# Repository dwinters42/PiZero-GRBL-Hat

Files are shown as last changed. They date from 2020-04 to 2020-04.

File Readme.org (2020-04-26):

#+TITLE:  Pi Zero GRBL hat

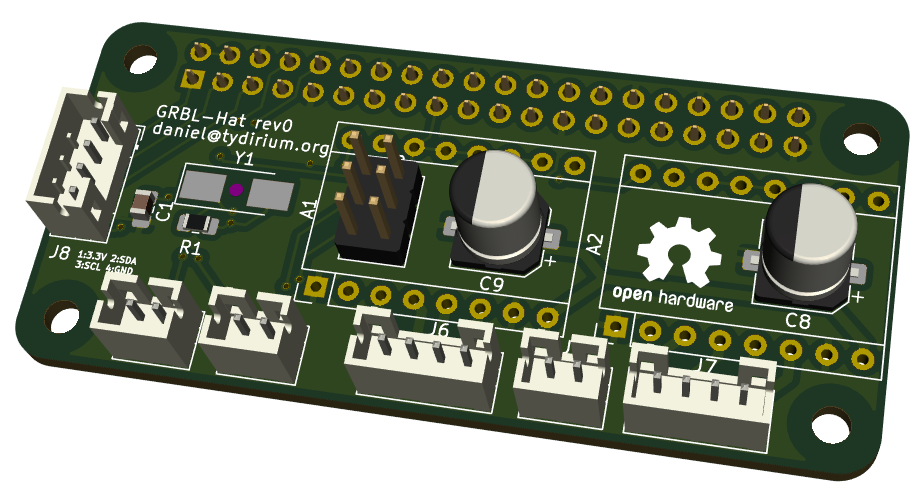
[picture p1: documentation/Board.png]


This is a RaspberryPi Zero-compatible add-on board that can be used to
control up to 2 stepper motors using GCode commands. The board works
with the non-Wifi (Pi Zero) and the Wifi version (Pi Zero W). It
should also work with a standard Raspberrypi, although I have not
tested this.

The hat has an on-board AVR Mega328P micro-controller that runs the
[[https://github.com/grbl/grbl][GRBL]] firmware, 2 sockets for Pololu-compatible Stepper boards
(e.g. DRV8825 and compatible) and connectors for the stepper motors,
limit switches, stepper motor power and an extra I2C connector that is
wired to the Pi Zero I2C contacts.

The big benefit of this arrangement is that the AVR takes care of all
the timing-sensitive tasks, so that the Raspberry Pi can do other
things.

* Building instructions
** Get components

See the bill of materials below.

** Assemble board

Use the brilliant interactive [[file:documentation/bom_interactive.html][HTML-BOM]] generated by the brilliant [[https://github.com/openscopeproject/InteractiveHtmlBom][BOM
KICAD plugin]] from openscopeproject to populate the board.

** Program firmware on AVR

Make sure the populated board is not connected to the Raspberrypi. Use
the ICSP connector on the front of the board to upload the GRBL
firmware using e.g. avrdude and a compatible programmer.

** Mount the board

With the Raspberrypi turned off, plug the GRBL hat board into the Pi
header, so that the 2 boards are aligned to each other. Do not connect
anything to the GRBL hat yet.

** Set up Pi Zero

In order for the communication to work, the on-board serial board of
the Raspberrypi has to be enabled with raspi-config: run raspi-config
in a terminal, go to Interfacing Options -> Serial -> No to login
shell -> Yes to enable serial port hardware. After rebooting, you
should have a new serial port accessible as /dev/ttyS0.

** Test serial connection

Connect to Grbl using the serial terminal of your choice. Set
the port to /dev/ttyS0 and the the baud rate to 115200, 8 bits, no
parity, 1 stop bit (8N1). One possibility is to use miniterm:

#+begin_example
  miniterm /dev/ttyS0 115200
#+end_example

Once connected, you will not see anything (GRBL started when the Pi
was plugged into power).

Type $ and press enter to have GRBL print a help message. You should
not see any local echo of the $ and enter. Grbl should respond with:

#+begin_example
  [HLP:$$ $# $G $I $N $x=val $Nx=line $J=line $SLP $C $X $H ~ ! ? ctrl-x]
  ok
#+end_example

Congratulations, you have a working GRBL controller connected to your
Pi Zero!

Shut down the Pi and disconnect power. Next, connect two stepper
driver boards (e.g. 2x Pololu DRV8825 driver board). Make sure you get
the orientation correct.

Then connect the motor power supply and set the current using the
trimpot on the driver boards. Disconnect motor power, plug in 2
stepper motors (e.g. NEMA17 form factor) and apply motor power again.

** First trial run

Turn on power to the Pi and log in via ssh. Run the following commands
from a terminal to test the motors:

#+begin_example
  stty -F /dev/ttyS0 115200 # set baud rate to 115200 baud
  cat testing/test.gcode > /dev/ttyS0
#+end_example

This should move first the x-axis to 45 degrees and back, followed by
the y-axis. If there is jerky motion or no motion at all, make sure
that the wire connections to the steppers are good.

* Using the board

The Raspberrypi board communicates with the GRBL controller over the
on-board serial port /dev/ttyS0. The serial port needs to be
configured to 115200 baud, 8 databits, 1 stopbit, no parity (8N1).

The stepper resolution is set to 32 microsteps in hardware, this
cannot be changed. For a standard stepper with 200 steps per
revolution this gives 200*32/360 = 17.778 steps per degree.

Look at the [[https://github.com/gnea/grbl/wiki][GRBL wiki]] for any GRBL related questions.

* Bill of materials

| *Ref* | *Qty* | *Value*          | *Part*                      | *Mouser part*     |
|-------+-------+------------------+-----------------------------+-------------------|
| A1    |     1 | AXIS_X           | Pololu DRV8825 module       |                   |
| A2    |     1 | AXIS_Y           | Pololu DRV8825 module       |                   |
| C1 C2 |     2 | 100n 0805        |                             |                   |
| C4 C5 |     2 | 33p 0805         |                             |                   |
| C8 C9 |     2 | 100u dia 6.3 25V |                             |                   |
| J1    |     1 | GPIO_CONNECTOR   | pin header 2x20             |                   |
| J2    |     1 | ISP              | pin header 2x03             |                   |
| J3    |     1 | LIMIT_X          | JST PH B2B 1x02 vert        |                   |
| J4    |     1 | LIMIT_Y          | JST PH B2B 1x02 vert        |                   |
| J5    |     1 | VMOT             | JST PH B2B 1x02 vert        |                   |
| J6    |     1 | MOTOR_X          | JST PH B2B 1x04 vert        |                   |
| J7    |     1 | MOTOR_Y          | JST PH B2B 1x04 vert        |                   |
| J8    |     1 | I2C              | JST PH B2B 1x04 vert        |                   |
| R1    |     1 | 1M 0805          |                             |                   |
| R2    |     1 | 10K 0805         |                             |                   |
| U1    |     1 | uC TQFP-32       | Microchip ATmega328P-AU     | 556-ATMEGA328P-AU |
| Y1    |     1 | 16MHz ABM3       | Abracon ABM3-16.000MHZ-B2-T | 815-ABM3-16-D2Y-T |

* Todos for next revision

- [ ] use less pins on the Raspi connector + cutout in PCB
- [ ] add photos of the finished board

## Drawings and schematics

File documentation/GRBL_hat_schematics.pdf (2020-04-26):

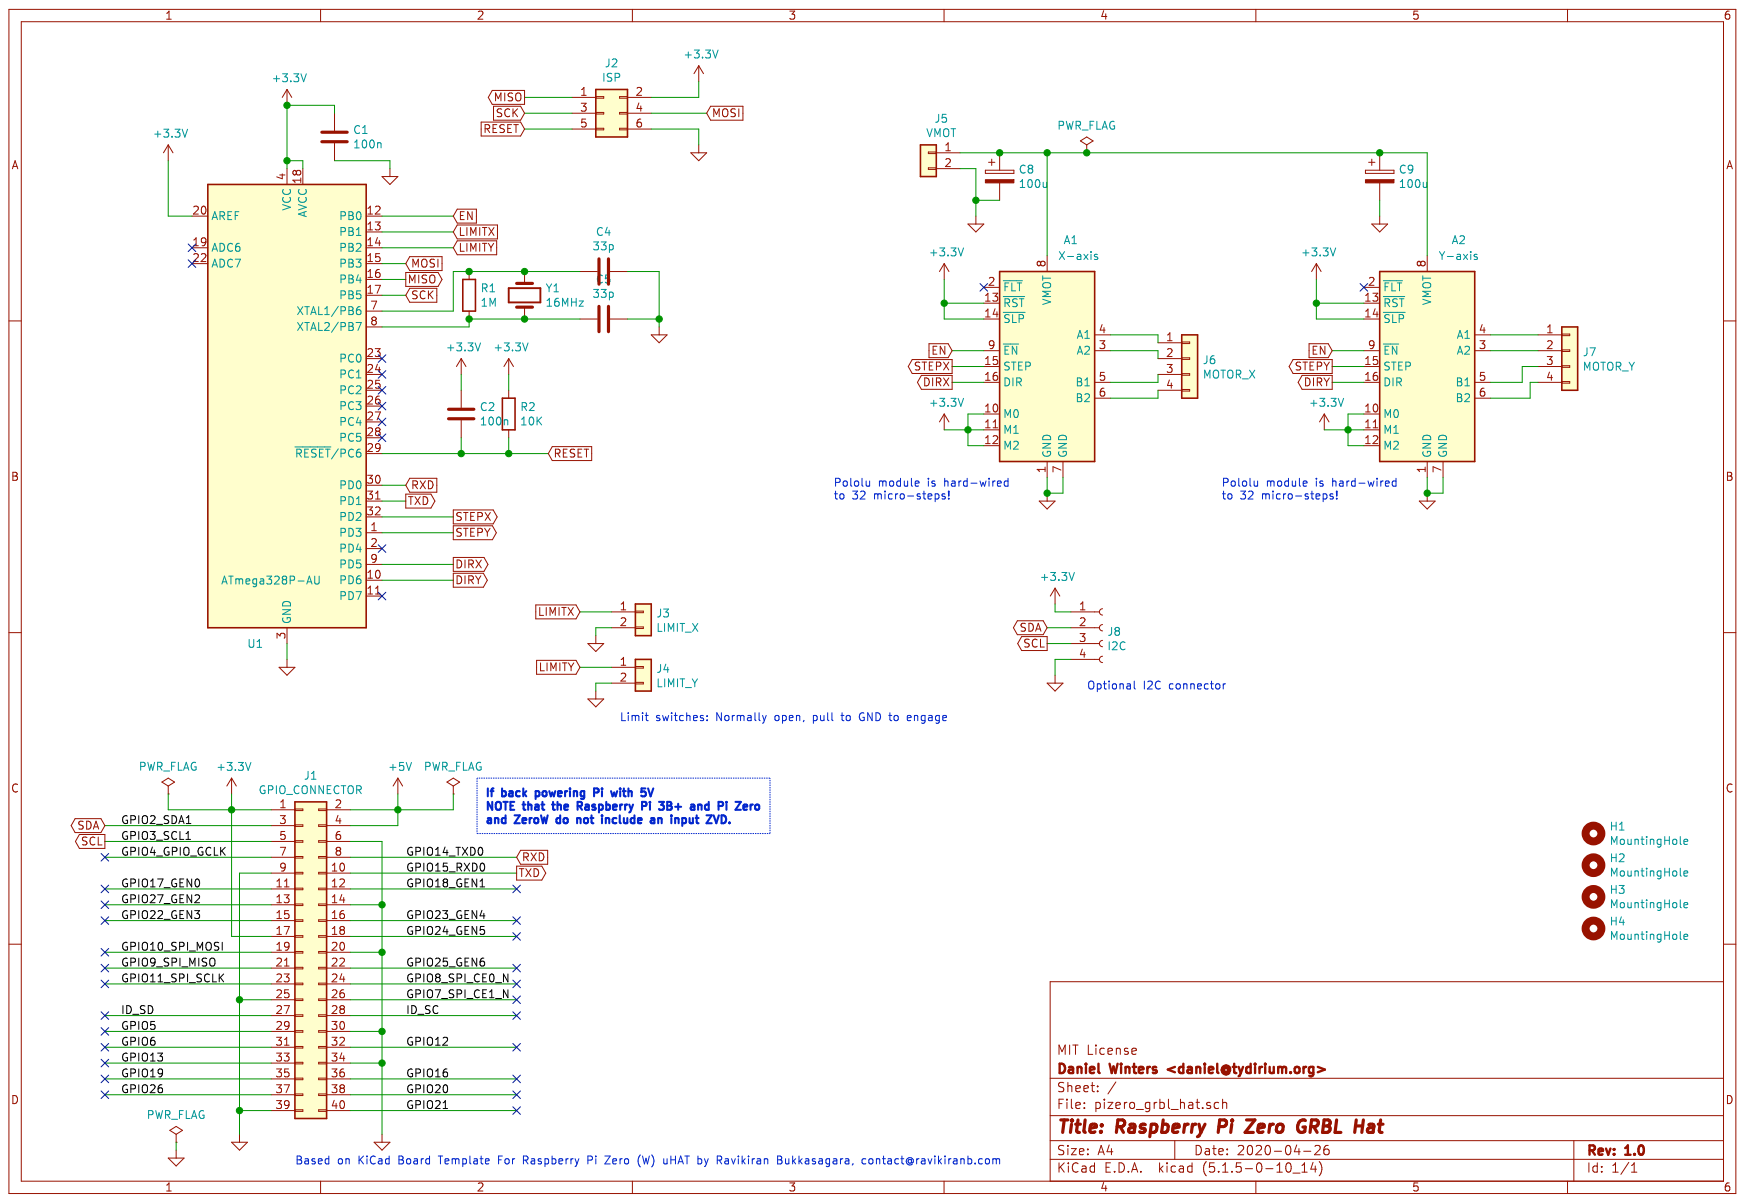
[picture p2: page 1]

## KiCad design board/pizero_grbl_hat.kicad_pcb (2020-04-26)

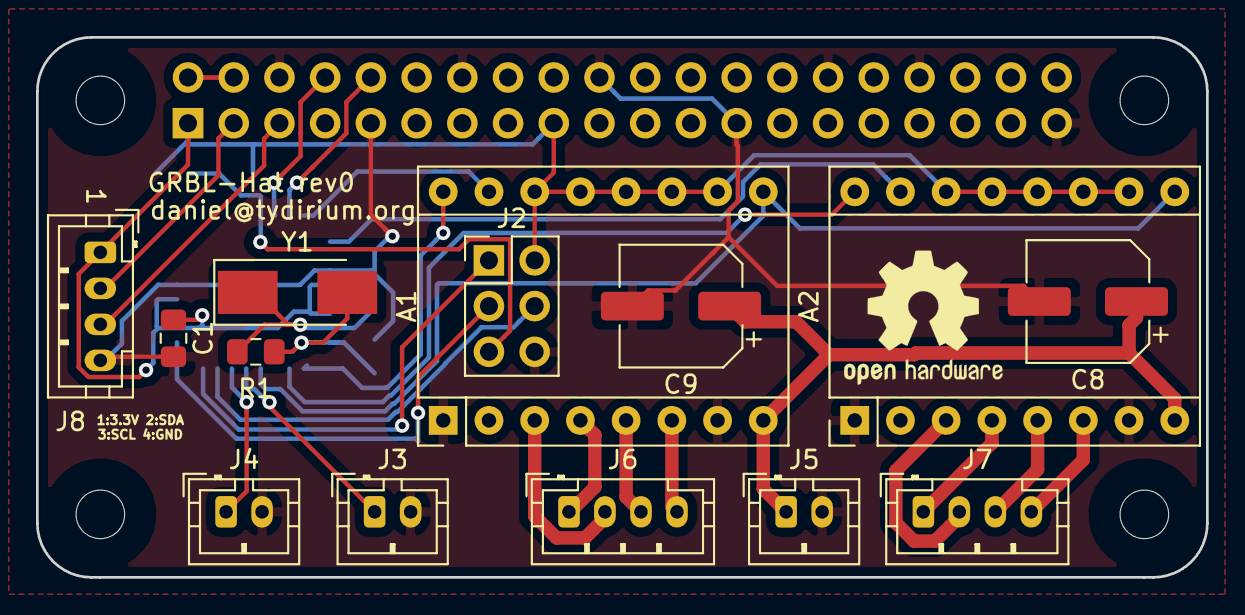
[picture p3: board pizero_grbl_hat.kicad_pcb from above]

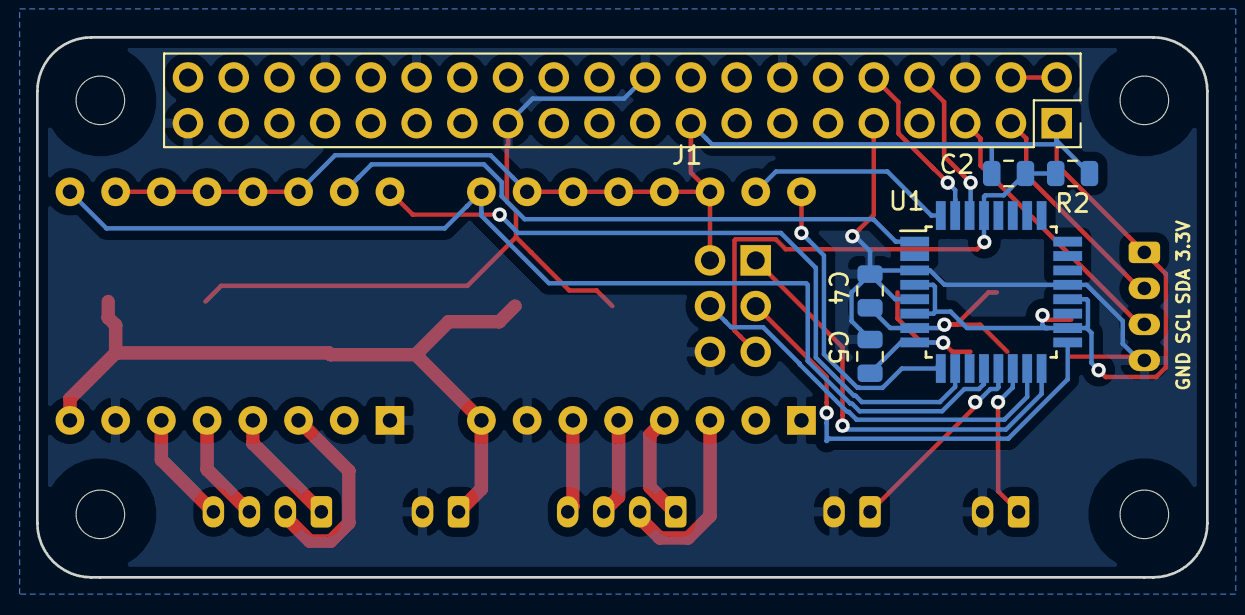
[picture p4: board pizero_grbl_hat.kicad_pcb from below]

Board: 2 copper layers, 65.0 x 30.0 mm, 24 parts (6 on the bottom side), 29 nets.

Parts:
A1: X-axis; Pololu_Breakout-16_15.2x20.3mm
A2: Y-axis; Pololu_Breakout-16_15.2x20.3mm
C1: 100n; C_0805_2012Metric_Pad1.15x1.40mm_HandSolder
C2: 100n; C_0805_2012Metric
C4, C5: 33p; C_0805_2012Metric
C8, C9: 100u; CP_Elec_6.3x7.7
H1, H2, H3, H4: MountingHole; MountingHole_2.7mm_M2.5_uHAT_RPi
J1: GPIO_CONNECTOR; PinSocket_2x20_P2.54mm_Vertical_Centered_Anchor
J2: ISP; PinHeader_2x03_P2.54mm_Vertical
J3: LIMIT_X; JST_PH_B2B-PH-K_1x02_P2.00mm_Vertical
J4: LIMIT_Y; JST_PH_B2B-PH-K_1x02_P2.00mm_Vertical
J5: VMOT; JST_PH_B2B-PH-K_1x02_P2.00mm_Vertical
J6: MOTOR_X; JST_PH_B4B-PH-K_1x04_P2.00mm_Vertical
J7: MOTOR_Y; JST_PH_B4B-PH-K_1x04_P2.00mm_Vertical
J8: I2C; JST_PH_B4B-PH-K_1x04_P2.00mm_Vertical
R1: 1M; R_0805_2012Metric_Pad1.15x1.40mm_HandSolder
R2: 10K; R_0805_2012Metric
U1: ATmega328P-AU; TQFP-32_7x7mm_P0.8mm
Y1: 16MHz; Crystal_SMD_Abracon_ABM3-2Pin_5.0x3.2mm_HandSoldering

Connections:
+3V3: A1.10, A1.11, A1.12, A1.13, A1.14, A2.10, A2.11, A2.12, A2.13, A2.14, C1.1, C2.1, J1.1, J1.17, J2.2, J8.1, R2.1, U1.4, U1.6, U1.18, U1.20
+5V: J1.2, J1.4
DIRX: A1.16, U1.9
DIRY: A2.16, U1.10
EN: A1.9, A2.9, U1.12
GND: A1.1, A1.7, A2.1, A2.7, C1.2, C4.1, C5.1, C8.2, C9.2, J1.6, J1.9, J1.14, J1.20, J1.25, J1.30, J1.34, J1.39, J2.6, J3.2, J4.2, J5.2, J8.4, U1.3, U1.5, U1.21
LIMITX: J3.1, U1.13
LIMITY: J4.1, U1.14
MISO: J2.1, U1.16
MOSI: J2.4, U1.15
unnamed: A1.3, J6.2
unnamed: A1.4, J6.1
unnamed: A1.5, J6.3
unnamed: A1.6, J6.4
unnamed: A1.8, A2.8, C8.1, C9.1, J5.1
unnamed: A2.3, J7.2
unnamed: A2.4, J7.1
unnamed: A2.5, J7.3
unnamed: A2.6, J7.4
unnamed: C4.2, R1.1, U1.7, Y1.1
unnamed: C5.2, R1.2, U1.8, Y1.2
RESET: C2.2, J2.5, R2.2, U1.29
RXD: J1.8, U1.30
SCK: J2.3, U1.17
SCL: J1.5, J8.3
SDA: J1.3, J8.2
STEPX: A1.15, U1.32
STEPY: A2.15, U1.1
TXD: J1.10, U1.31

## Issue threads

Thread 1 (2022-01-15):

Quick question about three drivers

javl, 2022-01-15:
Just a quick question: did you use two stepper drivers just because you only needed /could fit two of them? Just wondering before I adapt your design to fit one for the z-axis as well and it turns out to be some hardware limitation I've missed ;)

dwinters42, 2022-01-16:
Hi Jasper,

> Just a quick question: did you use two stepper drivers just because you only needed /could fit two of them? Just wondering before I adapt your design to fit one for the z-axis as well and it turns out to be some hardware limitation ;)
>
The reason that the board has only 2 stepper drivers is that I only needed 2 for a 2-axis gimbal I wanted to drive. GRBL on the ATmega328p supports 3 stepper, so no reason not to add a 3rd driver...

Let me know if you decide to design a 3-axis version!

Cheers,
Daniel

javl, 2022-01-17:
Thanks, I will. And thank you for putting all of the KiCad files online.

Closed 2022-01-17.

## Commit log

2019-11-20 initial import, work in progress
    [pizero_grbl_hat.kicad_pcb, pizero_grbl_hat.sch]
2019-11-20 finish schematics, start assigning packages
    [pizero_grbl_hat.sch]
2019-11-21 layout mostly done
    [pizero_grbl_hat.sch]
2019-11-27 finish layout and print schematics
    [pizero_grbl_hat.kicad_pcb, pizero_grbl_hat.sch]
2019-11-29 create BOM and start Readme
    [pizero_grbl_hat.csv]
2020-02-09 start working on rev1, work in progress
    [pizero_grbl_hat.kicad_pcb, pizero_grbl_hat.sch]
2020-02-09 move Kicad board files to a subdirectory
    [pizero_grbl_hat.kicad_pcb, pizero_grbl_hat.sch]
2020-02-09 mv bill of materials around
    [pizero_grbl_hat.csv]
2020-02-09 move the schematics into a documentation folder
2020-03-20 show I2C pins on front and back silkscreen
    [pizero_grbl_hat.kicad_pcb]
2020-04-22 add open hardware logo on the board
    [pizero_grbl_hat.kicad_pcb]
2020-04-26 dome doc updates to schematics
    [pizero_grbl_hat.sch]
2020-04-26 use AVR symbol from the standard library instead of rescue lib
    [pizero_grbl_hat.kicad_pcb, pizero_grbl_hat.sch]
2020-04-26 move interactive bom to documentation/
2020-04-26 add a rendering of the board (without the Pololu modules)
2020-04-26 fix link to BOM

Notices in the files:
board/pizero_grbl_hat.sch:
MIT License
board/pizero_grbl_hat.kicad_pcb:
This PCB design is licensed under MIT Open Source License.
